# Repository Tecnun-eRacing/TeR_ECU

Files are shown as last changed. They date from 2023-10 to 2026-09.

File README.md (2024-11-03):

# TeR_ECU
TeR Electronic Control Unit, which handles the behaivour of the cars dynamic system while gathering all the sensor and data neccesary for operation through its inputs and communication buses.

## Features
- STM32F405VGTx Microcontroller (Cortex™-M4 Core@168mHz with FPU)
- USB For Diagnosis Operation
- 2x CAN 2.0 For its communication with the Powertrain CAN and main sensors CAN
- NEO M9N GPS modules from u-blox, for determining cars position (Posibility to drive an active Antenna)
- 9DOF IMU consisting in Accelerometer, Gyroscope and Magnetometer for accurate posting and torque algorithms
- 4 Digital Inputs (0V-24V Range)
- 4 PWM Outputs(3.3V), for servo control, including actuators
- 4 Analog Inputs (0V-3.3V) Possibility of configurable Input divider
- 4 Digital Outputs(0V-24V) High side mosfet drivers
- 2 WS2812 RGB Led Channels using integrated SPI for FS-Spain LightShow Acceleration


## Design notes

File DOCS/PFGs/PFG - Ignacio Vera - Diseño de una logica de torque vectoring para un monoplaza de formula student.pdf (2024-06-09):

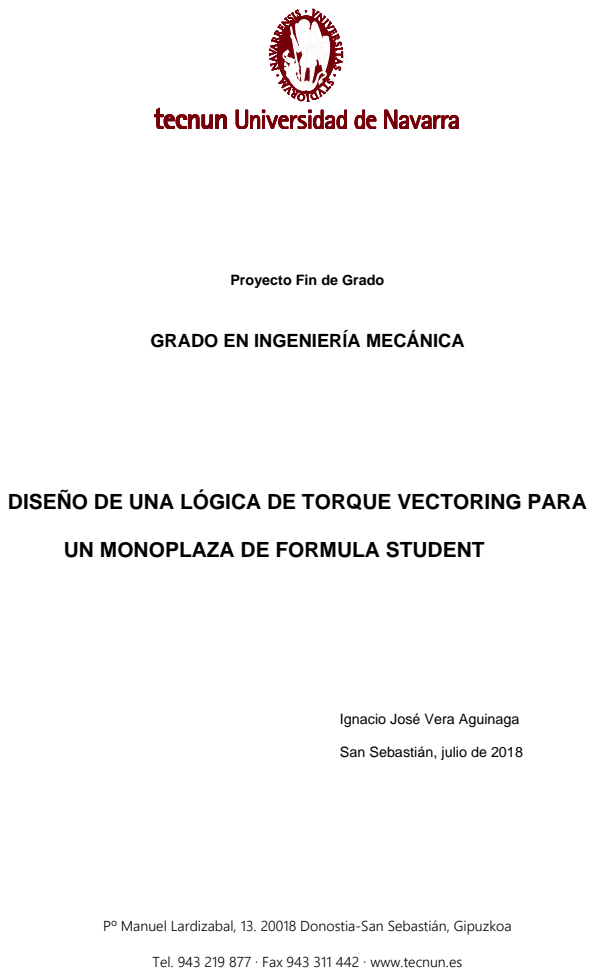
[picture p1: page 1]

Proyecto Fin de Grado

GRADO EN INGENIERÍA MECÁNICA

DISEÑO DE UNA LÓGICA DE TORQUE VECTORING PARA

UN MONOPLAZA DE FORMULA STUDENT

Ignacio José Vera Aguinaga

San Sebastián, julio de 2018

Pº Manuel Lardizabal, 13. 20018 Donostia-San Sebastián, Gipuzkoa

Tel. 943 219 877 · Fax 943 311 442 · www.tecnun.es

Diseño de un Torque Vectoring para un monoplaza de FSAE

Ignacio J. Vera Aguinaga

## AGRADECIMIENTOS

A mi familia, especialmente a mis padres y a mi hermano. Por aguantarme y

sufrirme cada día. Por darme absolutamente todo lo que son y tienen. Por estar a mi lado

incluso cuando las horas de trabajo no me permiten estar al suyo. No habría llegado hasta

aquí de no ser por ellos. Gracias, por todo.

A mis amigos. Por no olvidarse de mí, aunque estuviera desaparecido. Por todos

estos años y los que nos quedan. Gracias.

A los profesores y compañeros que he tenido, desde la Compañía de María,

pasando por SUMMA Aldapeta, la Universidad de Linköping y finalmente Tecnun. De todos

ellos he aprendido y me llevo cosas que hoy me hacen mejor persona. Gracias.

A Iker Aguinaga. Por todos sus consejos y por ayudarme a ver las cosas de otra

manera. Gracias.

A Andoni Medina. Por guiarme en la realización de este proyecto y estar siempre

dispuesto a echarme una mano. El contenido que aquí se recoge habría sido mucho peor

sin su ayuda. Gracias.

A mis amigos y excompañeros de Tecnun Motorsport. Por inculcarme una pasión.

Por los días de taller, y también por las noches. Por ayudarme a crecer en todos los

aspectos. GrAciaS.

A mis amigos y compañeros de Tecnun eRacing. Por mantener viva mi ilusión. Por

darme la oportunidad de realizar este proyecto, que espero que sea de utilidad en el futuro.

Por todo lo que nos queda por lograr y lograremos. Esto es en gran parte para vosotros.

Gracias.

## CONTENIDO

## ÍNDICE DE FIGURAS

Figura 57: Bloque E-Gas E-Motor correspondiente a la asignación de par motor de Carmaker for Simulink

Figura 82: Bloque Wheel Long v estimation | 108
Figura 83: Bloque K parameter | 109
Figura 84: Bloque Sigmoid function | 110
Figura 85: Resultados en la prueba de Endurance de FSG 2017 | 111

## ÍNDICE DE TABLAS

Tabla 1: Valores empleados para el cálculo de yaw rate | 42
Tabla 2: Parámetros del controlador PID | 57
Tabla 3: Presupuesto de inmovilizado | 77
Tabla 4: Presupuesto de material fungible | 77
Tabla 5: Presupuesto de equipamiento | 77
Tabla 6: Presupuesto de software | 78
Tabla 7: Presupuesto de mano de obra | 78
Tabla 8: Resumen del presupuesto | 79

## ÍNDICE DE GRÁFICOS

Gráfico 1: Puntuación FSAE | 17
Gráfico 2: Puntuación FSG | 18
Gráfico 3: Fuerza longitudinal frente a slip ratio (Hoosier R25B 16x6x10) | 32
Gráfico 4: Comparación del yaw rate objetivo y el real (sin TV) | 55
Gráfico 5: Par en los motores del vehículo (sin TV) | 55
Gráfico 6: Comparación del yaw rate objetivo y el real (con TV) | 58
Gráfico 7: Par en los motores del vehículo (con TV) | 59
Gráfico 8: Comparación de velocidades con y sin TV | 59
Gráfico 9: Comparación de aceleración lateral con y sin TV | 60
Gráfico 10: Comparación de % de acelerador pisado por el piloto con y sin TV | 61
Gráfico 11: Comparación del ángulo de giro de volante con y sin TV | 61
Gráfico 12: Comparación del yaw rate objetivo y el real en Skidpad (sin TV) | 63
Gráfico 13: Par en los motores del vehículo en Skidpad (sin TV) | 63

## RESUMEN

Este proyecto nace de la necesidad del equipo de Formula Student Tecnun eRacing

de mejorar continuamente y afrontar nuevos retos para conseguir los mejores resultados

posibles en competición.

En él se desarrolla el diseño de una lógica de torque vectoring. El torque vectoring

consiste en variar la asignación del par entregado a las ruedas de un vehículo de modo

independiente en función de las condiciones de condición, de un modo dinámico. De este

modo, se puede conseguir mejorar el comportamiento general del vehículo y hacerlo más

estable y rápido.

El proyecto se escribe de modo que pueda servir de guía a futuros estudiantes que

quieran profundizar en el campo del control orientado a la dinámica vehicular.

Primero se presentan los conceptos dinámicos básicos que han hecho de base para

el control, así como los requerimientos a nivel de sensorización para implementar un

algoritmo de torque vectoring en un monoplaza de FSAE.

Tras esto se describe en detalle el algoritmo de control empleado: un generador de

referencias de yaw rate que, combinado con un controlador PID, genera un valor de

incremento de par motor que se introduce en los dos motores eléctricos del TeR18. Las

simulaciones del algoritmo, realizadas en IPG Carmaker, muestran una mejora en el tiempo

por vuelta de hasta 1,63 segundos en la prueba de Endurance.

El resultado final del proyecto es un algoritmo de control realizado en Simulink y

listo para ser implementado en el monoplaza de Tecnun eRacing.

## 1 INTRODUCCIÓN

### 1.1 La Formula Student

La Formula Student es una competición internacional entre escuelas de ingeniería,

consistente en formar un equipo de estudiantes para diseñar, fabricar, montar y preparar

un monoplaza de carreras para participar en una serie de pruebas, celebradas en algunos

de los circuitos de automovilismo más célebres del mundo.

La competición de la Formula Student nació de la mano de la SAE (Society of

Automotive Engineering). Conocida como Formula SAE o FSAE, la categoría se desarrolla

en eventos oficiales organizados anualmente.

Figura 1: Logotipo de la SAE

Algunos ejemplos de competiciones oficiales son:

- Formula SAE Michigan, organizado por SAE International
- Formula SAE Australasia, organizado por SAE Australasia
- Formula SAE Italy, organizado por ATA
- Formula Student UK, organizado por IMechE
- Formula Student Austria, organizado por Formula Student Austria
- Formula Student Germany, organizado por FSG e.V.
- Formula Student Spain

Figura 2: Formula Student Germany 2017

Para garantizar unos requisitos de seguridad y buenas prácticas de diseño,

fabricación y mantenimiento, es necesario que los vehículos participantes cumplan una

extensa normativa para poder participar. Antes de que el coche pueda participar en ninguna

prueba dinámica, los jueces de la competición han de acreditar que cumple con dichas

normas.

Esta competición supone una gran oportunidad para estudiantes de ingeniería de

poner en práctica los conocimientos adquiridos en las clases. Además, es también una

oportunidad para acercarse al mundo de la competición del motor.

1.1.1 La competición

Las competiciones de Formula Student valoran tanto aspectos estáticos como dinámicos del monoplaza en los días que dura la competición. Ésta no consiste única y

exclusivamente en hacer rodar el coche para obtener el mejor tiempo posible, sino que

valora y juzga las decisiones tomadas por los estudiantes para lograr su monoplaza.

Los eventos estáticos son todos aquellos eventos puntuables para la clasificación

final que se realizan con el coche parado. Dichos eventos son el Cost Report, un análisis

del coste total del vehículo, el Business Plan, una preparación del presupuesto una

presentación sobre el marketing y finalmente el Design Report, una defensa del diseño del

vehículo completo ante un tribunal especialista en el sector de la automoción.

Los eventos dinámicos son los siguientes: la Acceleration, una carrera de

aceleración en una recta de 75m, el Skidpad, una prueba consistente en dar varias vueltas

a un circuito con forma de “8” para probar el comportamiento del vehículo en situaciones

de alta aceleración lateral y medir su agarre, el Autocross, una prueba consistente en dar

dos vueltas a un circuito revirado que valora la agilidad del vehículo, y la Endurance, una

carrera de resistencia en la que el coche tiene que completar 22 km con un cambio de

piloto a mitad de prueba.

Finalmente, el consumo del coche se valora en la prueba de Efficiency. En esta

prueba se obtienen puntos en función del consumo total de combustible del monoplaza en

la Endurance.

1.1.2 Puntuación de las competiciones

La distribución actual de la puntuación de la competición es diferente en las

competiciones organizadas por la FSAE y las que dependen de la normativa de Formula

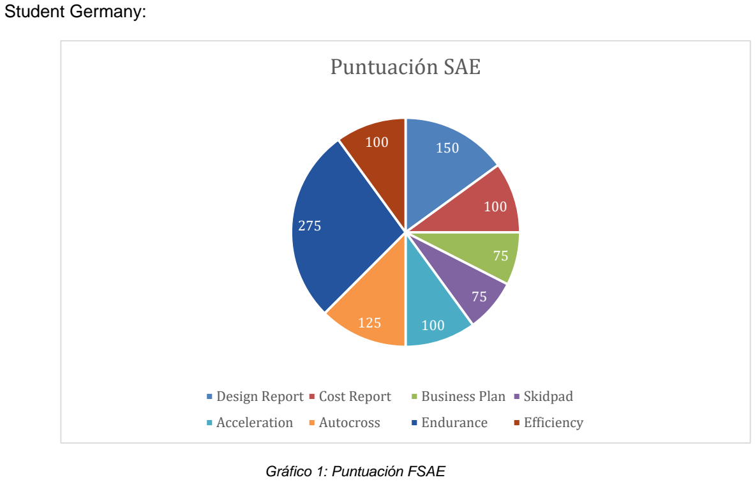
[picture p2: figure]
Student Germany:; Gráfico 1: Puntuación FSAE; Puntuación SAE; Design Report; Cost Report; Business Plan; Skidpad; Acceleration; Autocross; Endurance; Efficiency

Así pues, la máxima puntuación que puede obtener cada equipo es de 1000 puntos.

En ambos formatos el reparto entre las pruebas estáticas y las dinámicas es el mismo,

siendo las pruebas estáticas aproximadamente un tercio de la puntuación total.

1.1.3 Historia de la Formula Student en Tecnun

La Escuela Superior de Ingenieros de la Universidad de Navarra (Tecnun) participa

en la Formula Student desde el año 2009. Con sede en el campus de Ibaeta, San

Sebastián; el equipo Tecnun Motorsport desarrolló anualmente un prototipo para competir

en la disciplina de vehículos de combustión hasta el año 2017. Con sede en el campus de

Miramón, el equipo Tecnun SEED Racing desarrolló un prototipo de propulsión eléctrica

desde 2011 a 2017.

En septiembre de 2017, y de la fusión de los anteriores, nació en Tecnun un nuevo

equipo de Formula Student: Tecnun eRacing. Este proyecto aúna los conocimientos de

Tecnun Motorsport y Tecnun SEED Racing para construir un monoplaza con el que

competir en la categoría de vehículos eléctricos.

Desde que los inicios de la Formula Student en Tecnun han pasado nueve

prototipos diferentes por el Laboratorio de Automoción de la Escuela, y siete por el

Laboratorio de Propulsión Eléctrica, con el objetivo de mejorar el diseño y con ello los

resultados año tras año. Puesto que las necesidades de la competición exigen fabricar un monoplaza desde cero cada año, el factor económico es de una importancia similar al

técnico a la hora de influir en el éxito de un monoplaza. Por esto, el equipo también se

dedica a buscar patrocinadores que puedan servir de apoyo para hacer frente a los costes

del proyecto.

El equipo está formado por alrededor de 50 alumnos bajo la supervisión de un

profesor encargado, organizado en dos departamentos principales, departamento de

organización y departamento técnico. Este último se divide en 6 áreas diferentes. Cada una de ellas, liderada por uno o dos Jefes de Área, se centra en una parte específica del

coche: electrónica de alto voltaje, electrónica de bajo voltaje, chasis, aerodinámica,

transmisión y suspensión.

Monoplazas de la FSAE construidos por Tecnun Motorsport:

Figura 3: Fstec 09 | Figura 4: Fstec 10
Figura 5: Fstec 11 | Figura 6: Fstec 12

Figura 7: Fstec 13 | Figura 8: Fstec 14
Figura 9: Fstec 15 | Figura 10: Fstec 16

Figura 11: Fstec 17

Monoplazas de la FSAE construidos por Tecnun SEED Racing:

Figura 12: e-TEC MKI | Figura 13: e-TEC MKII
Figura 14: Fstec e-III | Figura 15: TSR 14
Figura 16: TSR 15 | Figura 17: TSR 16

Figura 18: TSR17

1.1.4 Tecnun eRacing

Esta temporada, de la unión de medios y capacidades de los equipos Tecnun SEED

Racing y Tecnun Motorsport, ha surgido un nuevo equipo, Tecnun eRacing, dedicado a la

fabricación de coches eléctricos de Formula Student.

Figura 19: El equipo de Tecnun eRacing

Uniendo los conocimientos de electrónica y propulsión eléctrica de Tecnun SEED

Racing y los conocimientos de dinámica vehicular, chasis, suspensión y aerodinámica de

Tecnun Motorsport, el equipo pretende seguir avanzando para obtener cada vez mejores

resultados en las competiciones a las que se presente.

## 2 MOTIVACIÓN Y OBJETIVOS

### 2.1 Motivación

La motivación para la realización de este proyecto es doble. En primer lugar, la

intención de lograr un coche lo más rápido posible que permita que Tecnun eRacing

consiga la mejor puntuación en competición. Como miembro del equipo, es deseo del autor

contribuir a que el monoplaza de Tecnun eRacing cuente con las tecnologías más

avanzadas que le permitan competir al máximo nivel.

En segundo lugar, se pretende abrir una vía al desarrollo de algoritmos de control

cada vez más avanzados y efectivos. La importancia creciente de mecanismos de control

de par en vehículos comerciales (controles de tracción, torque vectoring…) fomenta el

interés en profundizar en el conocimiento de dichas tecnologías.

### 2.2 Objetivos

El objetivo principal de este proyecto es diseñar, probar y validar una lógica de

control que, mediante la técnica de torque vectoring, mejore el desempeño del monoplaza

de Tecnun eRacing en las pruebas dinámicas de las competiciones de Fórmula Student a

las que acuda el equipo. También se trabajará en el desarrollo de un traction control como

complemento al torque vectoring.

Por mejorar el desempeño se entiende disminuir el tiempo en el que el coche realiza

cada prueba, para obtener así un mayor número de puntos y un mejor lugar en la

clasificación de la competición. Así, se considerará que la lógica de torque vectoring

programada es buena si se consiguen los siguientes resultados:

- Disminución de 2 segundos por vuelta el tiempo en las pruebas de Autocross

y Endurance.

- Disminución de 0,3 segundos por vuelta el tiempo en la prueba de Skidpad.

En la prueba de Acceleration el torque vectoring no actúa y no produce ningún

beneficio. Para conseguir disminuir el tiempo en esta prueba sería necesario diseñar un

control de tracción que minimice el deslizamiento de las ruedas del vehículo en aceleración.

Como se detalla más adelante, se ha tratado de diseñar dicha lógica sin éxito.

Podría realizarse un algoritmo capaz de tener un impacto positivo en la prueba de

Efficiency, introduciendo en la lógica los parámetros necesarios para aumentar el par de regeneración de los motores eléctricos del vehículo y minimizar el consumo de energía de

las baterías. Para no introducir una complicación excesiva en el presente proyecto, no se

ha tenido esto en cuenta a la hora de diseñar el TV.

Asimismo, se definen también una serie de objetivos cualitativos que derivan del

uso del torque vectoring:

- Conseguir un coche más sencillo de conducir: cuanto más fácil de entender

sea el comportamiento del vehículo para el conductor, más cómodo se

sentirá con el mismo y le permitirá circular a mayor velocidad y de una forma

más segura. El torque vectoring puede usarse para corregir el efecto

suubvirador o sobrevirador de un vehículo y lograr un coche neutro.

- Mantener el par por debajo del límite de tracción: controlando el par

entregado a cada rueda por debajo del límite de tracción de las mismas, se

asegura que las ruedas motrices no derrapan y por tanto no se

desaprovecha la potencia del vehículo, además de consumirse menos

energía.

## 3 ESTADO DEL ARTE

### 3.1 El torque vectoring

El torque vectoring (TV en forma abreviada) es un sistema para controlar el par en

las ruedas de un automóvil dependiendo de la situación de conducción.

En coches convencionales con motor de combustión interna este efecto se logra

por medio del diferencial. A ambos ejes de salida de un diferencial convencional se coloca

un sistema de discos de embrague accionado por un motor eléctrico y un conjunto de

engranajes. En una curva, los motores eléctricos accionan el embrague de la rueda

exterior, conectando un sistema de engranajes planetarios a la salida del diferencial. Esto

cambia la relación de transmisión en el semieje exterior, aumentando el par enviado a la

rueda exterior.

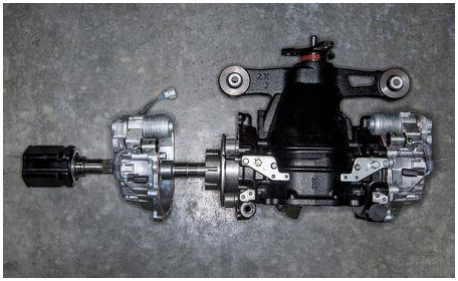
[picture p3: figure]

Figura 20: Diferencial con Torque Vectoring de un Lexus RC F

Esta misma técnica también se emplea en coches con tracción a las 4 ruedas para

regular el par que se envía al eje delantero o al trasero.

En coches eléctricos con más de un motor es más sencillo implementar el torque

vectoring ya que no requiere de ningún componente mecánico adicional: basta con

programar una lógica de control que altere la comanda de par que se envía a cada uno de

los motores.

Figura 21: Imagen del powertrain del TeR18, con dos motores Emrax 188

Además, en comparación con los diferenciales con TV, este sistema ofrece la

ventaja de permitir controlar de un modo mucho más preciso el par que se entrega a cada

rueda.

### 3.2 Torque vectoring en la Formula Student

Algunos de los equipos que participan en la categoría eléctrica de Formula Student

llevan años desarrollando diferentes lógicas de control para coches de tracción a dos o

cuatro ruedas. Principalmente se emplea para lograr tres objetivos:

- Ajustar el yaw rate del vehículo.
- Aumentar la aceleración lateral máxima.
- Controlar el slip ratio de las ruedas tractoras.

### 3.3 Torque vectoring en Tecnun

En los años de historia de la FSAE en Tecnun, se han realizado investigaciones por

parte del equipo Tecnun SEED Racing en el campo del Torque Vectoring, habiéndose

incluso realizado un Trabajo de Fin de Grado sobre la materia.

También se ha probado con sistemas de asignación de par sencillos como introducir

una variación de par proporcional al giro de volante en el monoplaza. Sin embargo, nunca

se llegó a implementar en ninguno de sus vehículos una lógica completa de control.

### 3.4 IPG Carmaker

Para la realización de este proyecto se ha empleado el software IPG Carmaker, de

la compañía IPG Automotive. Es un software popular en la industria del automóvil que

permite simular dinámicamente el comportamiento de un coche previamente modelado en

el programa.

Figura 22: Interfaz gráfica de IPG Carmaker

IPG Carmaker permite la definición de la mayoría de parámetros de un coche:

masas, rigideces, amortiguadores, neumáticos, geometría de suspensión… También es

posible generar un trazado de circuito o modelar características del piloto.

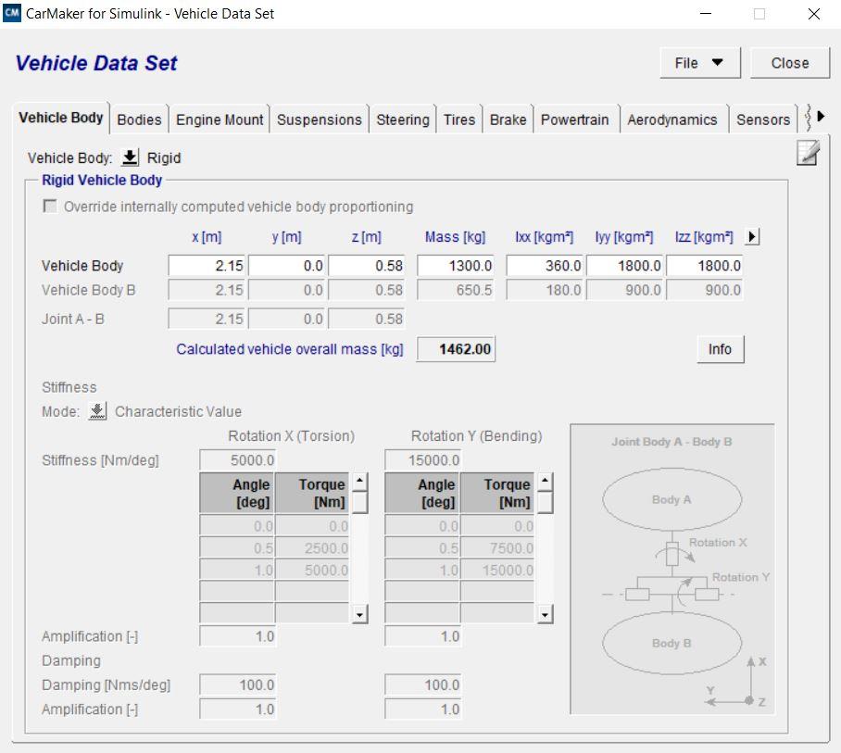
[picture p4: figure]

Figura 23: Muestra de algunos de los parámetros personalizables en Carmaker

En este proyecto se ha utilizado el modelo del TeR18 creado por el antiguo miembro

del equipo Carlos Rubio para su proyecto de Fin de Máster “Parametrization and Simulation

of an Electric FSAE Racecar”.

### 3.5 Simulink

El software elegido para programar la lógica de control ha sido Simulink, de la

compañía Mathworks. Se trata de un software de programación en bloques con una gran

variedad de funciones.

Figura 24: Ejemplo de programa de Simulink

Por ser un entorno basado en Matlab, es totalmente compatible con él, posibilitando

trabajar en Matlab con resultados obtenidos en Simulink.

IPG Carmaker posee una extensión llamada “Carmaker for Simulink”, mediante la

cual se puede trabajar con los modelos de Carmaker desde el entorno de Simulink,

alterando sus parámetros y añadiendo funciones mediante bloques programables. Gracias

a esto ha sido posible modificar el modelo de vehículo del que se disponía para introducir

en él el algoritmo de TV en forma de diagrama de bloques.

## 4 NOCIONES BÁSICAS DE DINÁMICA VEHICULAR

En este apartado se explicarán únicamente los conceptos de Dinámica Vehicular

necesarios para entender los razonamientos seguidos en este proyecto. Para una mayor

profundización en la Dinámica Vehicular, se recomienda acudir a los libros “Fundamentals

of Vehicle Dynamics”, de T. D. Gillespie, y “Race Car Vehicle Dynamics”, de Milliken y

Milliken.

### 4.1 Ejes de referencia

Para ser coherentes con la definición de las ecuaciones en la programación se ha

empleado el sistema de referencia indicado a continuación durante toda la realización del

proyecto:

Figura 25: Ejes de referencia empleados en el proyecto

El eje X coincide con el eje longitudinal del vehículo, siendo el sentido positivo hacia

el frente. El eje Y se encuentra en un plano horizontal, es perpendicular al eje X y pasa por

el centro de gravedad del coche, siendo el sentido positivo hacia la izquierda mirando el

vehículo desde arriba. Por último, el eje Z es el eje vertical que pasa por el CdG y su sentido

positivo se define hacia arriba.

### 4.2 El neumático

4.2.1 Slip ratio y slip angle

El neumático es uno de los componentes más importantes de un automóvil. Al ser

su único punto de contacto con el suelo, es el encargado de transmitir a la pista todas las

fuerzas que impulsan al vehículo en su movimiento.

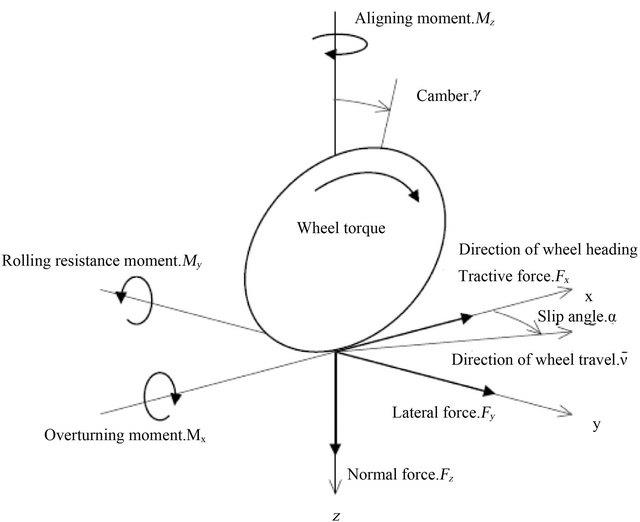
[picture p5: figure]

Figura 26: Fuerzas sobre una rueda

Normalmente, el movimiento de los neumáticos de un coche no es de rodadura

pura. Debido a la deformación que sufren los neumáticos durante el movimiento del

vehículo parte del área de contacto de los mismos desliza mientras la otra posee

movimiento de rodadura

Se define el slip ratio o ratio de deslizamiento como la relación entre la velocidad

angular real que posee una rueda y la que tendría en un movimiento de rodadura perfecta.

Hay diferentes maneras de definir el slip ratio, pero la empleada en este proyecto ha sido

la definida por la SAE:

SR =

ω × rw
v

− 1

Otro parámetro importante a definir es el slip angle o ángulo de deriva de una rueda,

el ángulo entre la dirección en la que apunta una rueda y la dirección en que realmente se

mueve. Este fenómeno ocurre debido a las deformaciones sufridas por el área de contacto

del neumático al ser sometido a una fuerza lateral.

Estos dos parámetros tienen una influencia directa y fundamental en las fuerzas

longitudinales y laterales que experimenta el vehículo. Para entender esto se explicará el

modelo de neumático.

4.2.2 Modelo de neumático

A finales del siglo XX Hans B. Pacejka desarrolló un modelo matemático capaz de

describir el comportamiento de un neumático en función de diversas variables, que se

conoce como “Fórmula Mágica de Pacejka”. Este modelo se ha ido actualizando en

distintas versiones y su uso está muy extendido. Con él se pueden calcular las principales

fuerzas que afectan a un neumático: longitudinal, lateral, combinadas, momento

autoalineante…

El modelo más avanzado tiene en cuenta las siguientes variables:

- Fuerza vertical
- Slip angle
- Slip ratio
- Camber angle
- Presión del neumático

Además, el modelo posee alrededor de 100 parámetros con significado físico propio

para caracterizar con precisión las propiedades de cada tipo de neumático.

Para realizar el modelo de los neumáticos se emplean los datos obtenidos por el

Tire Test Consorcium (TTC) y el software Optimum Tire. El TTC es una organización

dependiente de la SAE que nació de la necesidad de los equipos de Formula Student de

disponer de datos precisos sobre el comportamiento de sus gomas. Se dedica a testear

diferentes tipos de neumáticos de posible uso en competiciones FSAE para publicar los

resultados en una base de datos puesta a la venta.

El equipo dispone de un modelo de los neumáticos Hoosier R25B 18x6 - 10

realizado por Carlos Rubio. Aunque los neumáticos finalmente empleados en el monoplaza

han sido los Hoosier R25B 18x7,5 - 10 (1,5 pulgadas más anchos), de estas gomas no se

poseen datos por no haberse publicado los resultados del test TTC en el momento de la

realización del proyecto. Por tanto, se utilizará el citado modelo.

Gráfico 3: Fuerza longitudinal frente a slip ratio (Hoosier R25B 16x6x10)

En la imagen se observa cómo cambia la fuerza longitudinal que el neumático ejerce

sobre la pista en función del slip ratio de la rueda. Se observa que existe una zona alrededor

del 0 en la que el comportamiento es lineal, tras la cual el neumático se satura y alcanza

el valor máximo de fuerza que es capaz de transmitir. Tras este pico, el valor de Fx

disminuye ligeramente.

Dicho pico de fuerza suele estar situado en valores cercanos al 0,1 o 0,12 de slip

ratio, siendo el valor de pico exacto diferente para cada neumático. El slip ratio se calcula

con la velocidad en rueda, con lo que puede ser alterado mediante el par motor, y por tanto

es posible controlarlo mediante el traction control para mantener su valor cerca del punto

óptimo.

La fuerza lateral que soporta un neumático es principalmente función del slip angle

al que se ve sometido.

### 4.3 Círculo de fricción

Se denomina círculo de fricción al círculo ficticio cuyo radio es del valor de la fuerza

máxima que una rueda es capaz de soportar en cada dirección. Esta figura no es circular

en realidad, pero en muchos trabajos se simplifica y se toma por una forma circular.

Figura 27: Dibujo del círculo de fricción, con una fuerza de ejemplo

Los límites de agarre de un vehículo se calculan con el coeficiente de fricción

neumático-asfalto:

Fmax = μ × Fz

Por tanto, son función de la carga vertical sobre la rueda. No se explicará en esta

memoria las transferencias de carga vertical que experimenta un coche en su movimiento,

pero sí se resalta que, si se conoce el valor de la carga vertical, se puede tratar de estimar

los límites de agarre de cada rueda. Si al mismo tiempo se conocen las fuerzas longitudinal

y lateral reales en cada neumático, se puede determinar la fuerza extra que se puede

aplicar a cada rueda mediante la modificación del par motor para acercarse lo máximo

posible a dicho límite sin superarlo.

### 4.4 Comportamiento lateral de un vehículo

Como se ha explicado anteriormente, el TV es un recurso para la mejora del

comportamiento de un vehículo al tomar una curva. Por tanto, se explicarán a continuación

los conceptos necesarios para tener unas nociones básicas sobre el comportamiento de

un coche en curva.

4.4.1 Yaw angle y yaw rate

Se llama yaw angle al ángulo entre el eje longitudinal (x) del coche y un eje de

referencia en el plano xy. Por tanto, el yaw rate es la velocidad angular con la que cambia

este valor, es decir, la velocidad con la que el vehículo pivota alrededor de su eje Z. Al

tomar una curva, un coche posee una velocidad de yaw además de una velocidad

longitudinal y lateral. El yaw rate se calcula como sigue:

YR =

v
R

4.4.2 Modelo de bicicleta y ecuación de Ackerman

En dinámica vehicular, es habitual emplear una simplificación consistente en

considerar el automóvil como un vehículo de sólo dos ruedas, una delantera y una trasera.

De esta simplificación, conocida como modelo de bicicleta, se deducen algunas

expresiones de gran importancia para el análisis del comportamiento de un vehículo.

Figura 28: Esquema del modelo de bicicleta

Desarrollando las relaciones geométricas entre ángulos de la Figura 28 se puede

hallar una relación para calcular el giro de rueda necesario para negociar una curva:

δ =

L
R

+ (αf − αr)

Siendo L la batalla del coche, R el radio de la curva y αf y αr los slip angles delantero

y trasero respectivamente. Esta ecuación se puede desarrollar aún más realizando un equilibrio de momentos y mediante la relación existente entre la fuerza lateral del neumático

y el slip angle.

δ =

L
R

+ K × ay

Siendo K el gradiente de subviraje, un parámetro característico de cada vehículo

que puede determinarse experimentalmente.

4.4.3 Subviraje y sobreviraje

Se llama subviraje al efecto que se produce cuando un vehículo gira menos de lo

comandado por su conductor. Al caso contrario se lo denomina sobreviraje. Ambos son

efectos indeseados en la conducción.

Cuando el slip angle de las ruedas delanteras es mayor que el de las traseras, o lo

que es lo mismo, cuando K>0, un coche de batalla L necesita un mayor ángulo de giro para

tomar una curva de radio R, y se produce el efecto de subviraje. Cuando el slip angle de

las ruedas traseras es mayor que el de las delanteras (o K<0), un coche de batalla L

necesita un menor ángulo de giro para tomar una curva de radio R, y se produce

sobreviraje.

Figura 29: Subviraje y sobreviraje

Si K=0, el vehículo es neutro y, teóricamente, responde a las comandas de giro

recibidas sin desviaciones.

## 5 SENSORIZACIÓN DEL VEHÍCULO

El presente proyecto se centra en el diseño del torque vectoring, pero para posiblitar

su implementación en el monoplaza es indispensable tener unas nociones básicas sobre

los sensores que permitirán recibir la información necesaria para el funcionamiento del

algoritmo de control, así como del controlador en el que se introducirá la lógica.

La líder del área de Electrónica de Tecnun eRacing, Paula Martínez, será la

encargada de implementar el TV en el TeR18 dentro del marco de su PFG. Para ello

empleará un microcontrolador TMS320F28377S en una placa comercial, que puede ser

programado en lenguaje Simulink. Este controlador lee la información necesaria de los

sensores del vehículo por comunicación CAN. La señal del sensor inercial es leída por el

dispositivo UART.

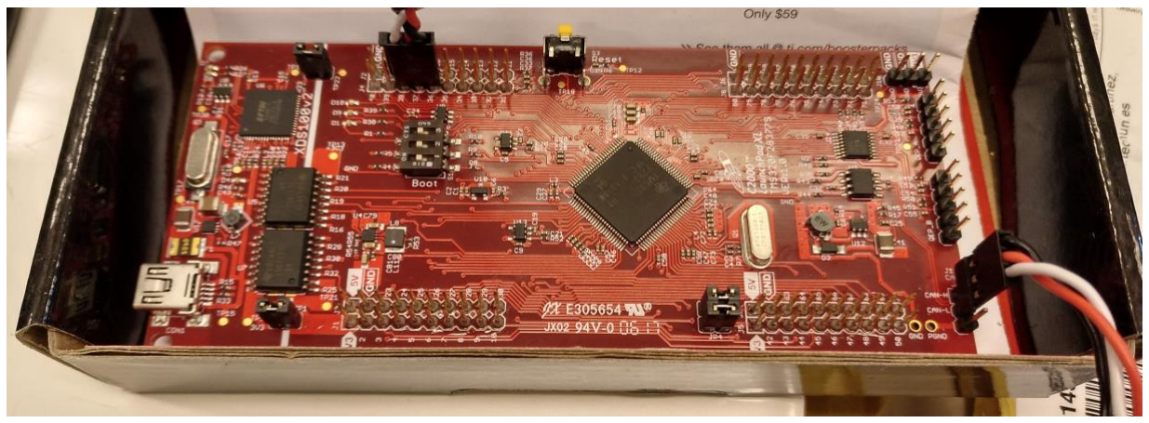
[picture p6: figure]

Figura 30: Placa comercial en la que se implementará el torque vectoring en el TeR18

Para obtener la información necesaria del vehículo en cada momento, se emplearán

los siguientes sensores:

- Sensor de giro de volante: este sensor viene integrado en la cremallera de

dirección, modelo Zedaro zRack 262. Se trata de un potenciómetro

conectado al eje que introduce el giro de la columna de dirección a la

cremallera. Por tanto, es capaz de medir el giro de esta última.

Figura 31: Sensor de giro de volante

- Inertial measurement unit (IMU): la IMU es un sensor capaz de medir

aceleraciones y velocidades, tanto lineales como angulares, en los tres ejes

de referencia del coche. En la imagen el sensor aparece en la posición en

la que se encuentra en el monoplaza: con los ejes en la orientación deseada.

Figura 32: Sensor inercial (IMU)

- Sensores de posición del acelerador: por normativa, se colocan en el pedal

del acelerador dos sensores de posición, que determinan la comanda de par

que es necesario enviar a los inversores.

Figura 33: Sensores de posición del acelerador

Estos son los sensores básicos para diseñar una lógica de torque vectoring efectiva.

Otros sensores que pueden instalarse para introducir funciones adicionales en la lógica

son:

- Sensor de presión de freno: mediante este sensor puede calcularse el par

de frenado en las ruedas traseras y alterar la comanda de par en

consecuencia, para que el par motor no trabaje contra los frenos.

Figura 34: Sensor de presión de freno

- Sensor de velocidad angular de motor/rueda: mediante estos sensores

puede calcularse el slip ratio de las ruedas o la potencia en las mismas,

conocida la comanda de par del motor. Los motores Emrax 188 que monta

el TeR18 llevan un sensor de velocidad integrado que puede usarse para

calcular la velocidad en las ruedas traseras con la relación de transmisión.

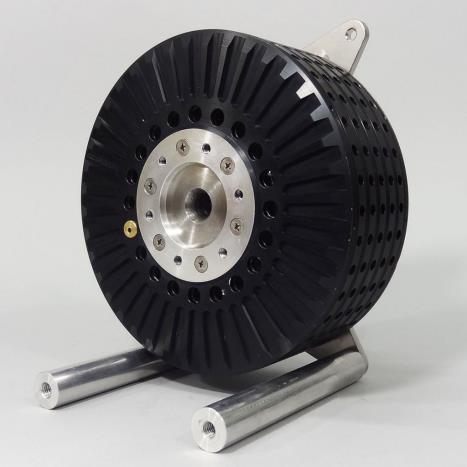
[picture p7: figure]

Figura 35: Sensor de velocidad en rueda | Figura 36: Motor Emrax 188
- | Galgas | extensiométricas | en | push/pull | rods: | instalando | galgas

extensiométricas para medir la deformación de los push rods de suspensión

pueden conocerse las cargas verticales en cada rueda en tiempo real. Este

dato es necesario para calcular las fuerzas en cada rueda usando el modelo

de neumático. La carga vertical también se puede determinar mediante

cálculos de dinámica vehicular.

Figura 37: Galgas extensiométricas en un test del Ferrari F138 (2013)

## 6 SISTEMA DE CONTROL

Durante la realización de este proyecto se han barajado distintas lógicas y

diferentes métodos para lograr los objetivos descritos en el apartado 2 de esta memoria.

Todos ellos se basan en la modificación de la señal de comanda de par, que se origina en

el sensor de posición del pedal del acelerador, accionado por el piloto.

Esta señal se puede interpretar en forma de tanto por 1, siendo 0 el valor cuando el

pedal no está siendo pisado y 1 cuando el piloto está acelerando a fondo. La lógica recibe

esta señal del pedal y la duplica, generando dos señales iguales del mismo valor que la

original. Después modifica cada una de esas dos señales de distinta manera para

finalmente enviar cada una a una rueda determinada.

La modificación de ese valor se realiza siguiendo el siguiente esquema:

Figura 38: Esquema del funcionamiento del sistema de control

Es importante respetar este orden y modificar la señal de par en función de las

solicitaciones en curva antes de modificarla para obtener el slip deseado. La razón para

esto es que, si se aplica el torque vectoring tras el traction control, es prácticamente

inevitable deshacer el efecto de control de slip dado por este último. Además, aplicando

primero el torque vectoring, puede estimarse la velocidad en cada rueda que el par motor

ya alterado conseguirá, usarse esa estimación para calcular el slip que tendrá cada

neumático contando la acción del TV y controlarlo.

## Datos de entrada

- Parámetros del
vehículo
(características
de la planta)
- Sensores (inputs
del piloto y
variables de
funcionamiento)

## Torque Vectoring

- Asignación del
par en rueda en
función de la
necesidad de
mejorar el
comportamiento
en curva

## Traction Control

- Corrección del
par obtenido en
el TV para cada
rueda para
conseguir la
máxima Fx o
evitar el
deslizamiento de
la rueda

### 6.1 Torque vectoring

La lógica de torque vectoring empleada consiste en la generación dinámica de un

valor de referencia de yaw rate que después se compara con el yaw rate real. Tras esto, el

error entre ambos es introducido en un PID cuya salida se traduce en incremento de par

motor, para tratar de aproximar el valor real de yaw rate a la referencia calculada

dinámicamente.

Los diagramas de bloques de Simulink correspondientes al TV se incluyen en el

anexo A1.

6.1.1 Cálculo del yaw rate ideal

Para este cálculo se emplean varios parámetros del coche y la información recibida

por diferentes sensores. Los datos necesarios son los siguientes:

Señal | Significado | Sensor | Valor
Gas | Porcentaje de acelerador pisado | Sensor de posición del pedal del acelerador | -
Ax | Aceleración longitudinal | IMU | -
Ay | Aceleración lateral | IMU | -
SteerAngle | Grados de giro del volante | Sensor de giro de volante | -
YawRate | Yaw rate | IMU | -
v | Velocidad | IMU | -
TVenable | Activador del TV | - | 0 o 1
Wheel rad | Radio de la rueda | - | 0,127 m
Wheelbase | Batalla del coche | - | 1,58 m
Track r | Ancho de vía trasero | - | 1,18 m
Gear ratio | Relación de transmisión en la reductora | - | 5
Steer Rack reduction | Relación desplazamiento cremallera – giro de volante | - | 5,25 mm/º
Steer TRod-Kingpin dist | Distancia del punto de anclaje del brazo de dirección en la mangueta al punto del eje de kingpin que está en el mismo plano horizontal | - 60 mm

Tabla 1: Valores empleados para el cálculo de yaw rate.

El cálculo se realiza de siguiente modo:

YRref =

v
L

× (δ − K × ay)

Donde:

- v es la velocidad del coche [m/s]
- L es la batalla del vehículo [m]
- δ es el ángulo de giro de la rueda [º]
- K es el gradiente de subviraje objetivo, elegido por el programador
- ay es la aceleración lateral del vehículo [g]

El valor δ se obtiene a partir del ángulo de giro de volante y las relaciones

geométricas de los movimientos de la dirección: al girar el volante se desplaza la

cremallera, lo que a su vez desplaza el conjunto de rueda haciéndolo pivotar alrededor del

eje de kingpin. El centro de pivotamiento es el punto del eje de kingpin que se encuentra

en el mismo plano horizontal que el anclaje del brazo de dirección a la mangueta, por lo

que el cálculo se realiza del siguiente modo:

δ = sin⁻¹ (

θ × StRack red
dist TRodKingpin)

Siendo θ el ángulo de giro de volante en grados.

Como el valor recibido de los sensores de ángulo de volante y aceleración lateral

viene dado en radianes y en m/s²
, respectivamente, hay que multiplicarlo por las

transformaciones correspondientes para operar con ellos en grados y g’s.

Este valor de referencia se multiplica después por una función de transferencia que

modela el tire relaxation length, el retraso temporal que se produce entre que la rueda

adquiere un slip angle determinado y la fuerza lateral del neumático adquiere un valor

estacionario. La función utilizada en el código es la definida en Carmaker para el relaxation

length.

6.1.2 Controlador PID

El valor de referencia de yaw rate, obtenido como se explica en el apartado anterior,

se resta después a la señal de yaw rate real para obtener el error en yaw, que será la señal

de entrada del controlador. El objetivo de todo este bloque de la lógica de control es

minimizar este error lo máximo posible, tratando de convertirlo en 0, ya que eso significará que el yaw rate real se aproxima lo máximo posible a la referencia calculada. Si el yaw rate

real es menor que la referencia es porque el coche subvira, mientras que si el yaw rate real

es mayor que la referencia el coche sobrevira.

Para ello se utiliza un controlador PID. Se ha optado por construir el controlador con

un sistema de bloques sencillos en vez de utilizar el bloque de controlador PID por defecto

de Simulink para lograr una mejor comprensión del controlador: poder construir el sistema

desde cero, visualizar la magnitud de cada una de sus señales, analizar mejor cómo

cambian al alterar sus parámetros…

El PID es un controlador que actúa en función a tres señales: el error, su integral y

su derivada. La primera de ellas proporciona una corrección mayor o menor según sea la

diferencia entre la referencia y el valor real mayor o menor, respectivamente. Si el error

alcanza un valor estable distinto de cero, la componente integral del controlador actúa para

tratar de reducirlo, y si la referencia varía mucho respecto del valor real en un período corto

de tiempo, la acción derivativa contrarresta ese cambio en el error.

Para visualizar las tres componentes de la forma más clara posible, se emplea la

forma paralela del controlador:

u(t) = Kp ∗ e(t) + Ki ∗ ∫ e(t) + Kd ∗

d [e(t)]
dt

Y, además, se definen

Ki =

Kp
Ti

Kd = Kp ∗ Td

Donde Ti y Td son el tiempo integral y derivativo, respectivamente. Definiendo estos

valores se definen también las ganancias integral y derivativa, como se muestra en las

fórmulas anteriores.

Las ganancias Kp, Kd y Ki definen la intensidad de las acciones proporcional, integral

y derivativa, aumentando o disminuyendo los efectos correctivos de cada una.

Para la acción integral se ha introducido además una función anti-Windup. El efecto

Windup ocurre cuando se da un cambio brusco en la referencia (cambio grande de valor

en un corto período de tiempo). Consiste en el aumento excesivo del valor de la acción

integral, provocando una salida del controlador demasiado elevada. Esto conlleva la aparición de un sobreimpulso que, si es demasiado grande, además de alejarnos de la

referencia puede provocar daños en el dispositivo actuador.

Figura 39: PID con anti-Windup

Para eliminar este efecto, las lógicas incluyen una serie de operaciones que

conforman la función anti-Windup: se introduce tras la suma de las tres señales una

saturación, y se resta el valor previo a la saturación a su valor posterior. Esta nueva señal

se multiplica por una ganancia y se suma al valor de la acción integral antes de su

integración. Si la actuación no supera el valor marcado por los límites de la saturación la

acción correctiva del anti Windup es 0, ya que la señal antes y después de la saturación

son del mismo valor y se anulan al restarlas.

De este modo, si el valor de la acción integral se dispara, la saturación limita el valor

de la suma de las tres acciones al valor máximo de actuación deseado. La señal sin saturar

se resta a la saturada, resultando una señal de valor muy alto y negativo que se multiplica

por una ganancia Kb y después se suma a la acción integral para devolverla a valores

normales (más bajos) en la siguiente iteración.

A continuación se explica de modo esquemático su funcionamiento:

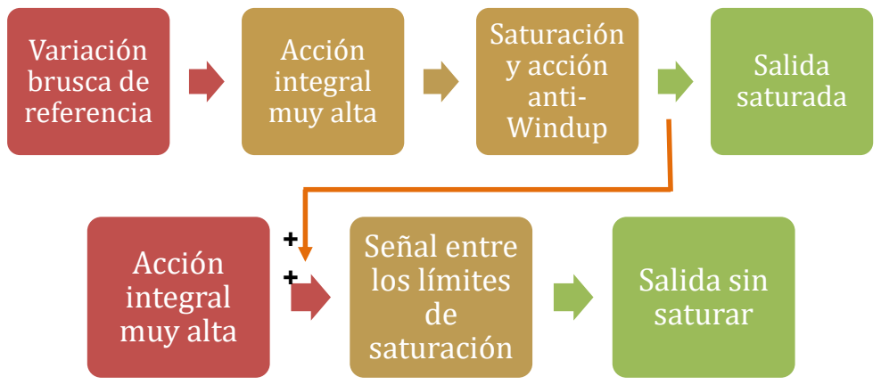
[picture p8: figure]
Variación brusca de referencia; Acción integral muy alta; Saturación y acción anti- Windup; Salida saturada; Señal entre los límites de saturación; Salida sin saturar

Figura 40: Esquema explicativo de la función anti-Windup

En la acción derivativa es necesario instalar un filtro para que la señal no presente

picos que distorsionen el valor de la actuación. Como la lectura que proviene de los

sensores tiene ruido, el valor del yaw rate real y el de referencia (calculado con datos de

sensores) también presentarán este ruido y por ende también aparecerá en el error. Por

tanto, la derivada de esta señal serán picos muy grandes de alta frecuencia.

Para eliminar estos picos, se instala un filtro pasa-baja a la salida del derivador,

precedido de una ganancia. La señal filtrada se resta de nuevo a la salida del derivador, y

se manda a la actuación la salida de la ganancia, como se muestra en el esquema:

Figura 41: Esquema de un PID con filtro derivativo

1

2

6.1.3 Controlador feedforward

El feedforward es un controlador que proporciona una señal de respuesta

puramente proporcional a la referencia o a la perturbación del sistema. En este caso, se

introdujo para poder tener un control de la respuesta dependiente de la referencia de yaw

rate además de tener uno proporcional al error.

Figura 42: Esquema de un controlador feedforward en paralelo con un controlador feedback

En caso de querer anular el controlador feedforward, basta con definir su ganancia

como 0.

6.1.4 Cálculo del incremento de par en rueda

El PID y el feedforward se tunearán de modo que su salida sea directamente un

valor en Nm, el incremento de Mz necesario para conseguir el yaw rate objetivo. Este valor

se transforma en incremento de par en rueda mediante una serie de sencillas operaciones.

Primero, se transforma el incremento de Mz necesario en incremento de Fx

necesario, dividiéndolo entre la mitad de la longitud del eje trasero. Desarrollando un poco

la expresión:

Inc Fx =

2 × Inc Mz
tr

Se podría considerar que el incremento en Mz se consigue aumentando la fuerza

en sólo una de las ruedas del vehículo. Sin embargo, esto podría significar la introducción

de un par excesivo en una de las ruedas, lo cual podría hacer derrapar esa rueda o incluso

dañar el propio motor al exigirle transmitir un par demasiado alto.

Por tanto, se opta por definir un nuevo incremento objetivo de fuerza longitudinal

como la mitad del anterior, y sumarlo en la rueda exterior y restarlo en la interior. De este

modo se obtiene un incremento total de Mz equivalente al que se obtendría sumando todo

el par en la rueda exterior disminuyendo el riesgo de que ocurran los incidentes antes mencionados. Otra ventaja de optar por esta estrategia es que, al disminuir la fuerza

longitudinal en la rueda exterior, estará más lejos del valor de fuerza combinada para el

cual el neumático pierde agarre. Por tanto, será capaz de absorber más fuerza lateral al

tomar una curva, aumentando la aceleración lateral del coche. Así,

Inc Fx ′ =

Inc Fx
2

Multiplicado por el radio de la rueda, se obtiene el valor necesario de par en rueda

del vehículo:

Inc Tw = Inc Fx ′ ∗ rw

Y para finalizar, dividiendo el valor del par en rueda entre la relación de transmisión

se obtiene el par motor que hay que sumar a la rueda exterior y restar a la interior.

Inc Tm =

Inc Tw
GR

Para poder sumar siempre el par a la rueda exterior y restarlo a la exterior

indistintamente de si son la rueda izquierda o derecha en cada caso, se utiliza el criterio de

signos definido en el apartado 4 y se aprovechan los signos de las lecturas obtenidas por

los sensores. Así, como el criterio utilizado implica que al tomar una rotonda los signos de

todos los parámetros son positivos, el incremento de par motor se suma a la rueda derecha

y se resta a la izquierda, porque la derecha es la rueda exterior al tomar una rotonda. Así,

si la curva es a derechas (sentido contrario a la toma de una rotonda), el incremento de par

motor será negativo y el par se sumará en la rueda izquierda y se restará en la derecha.

También se ha colocado un filtro pasa-baja en la señal de incremento de par, para

evitar que se den transferencias bruscas de par entre los dos motores del coche mientras

está en marcha.

Cabe destacar que todos los efectos se han descrito teniendo en cuenta que el

coche subvira y por tanto el error en el PID es positivo. Si el coche sobrevirase, el error

sería negativo y los incrementos de par se darían en sentido contrario.

Además, se ha introducido una medida de seguridad al incremento de par del torque

vectoring: un enable en forma de puerta lógica que devuelve 0 si el piloto no está pisando

el acelerador y 1 si lo está haciendo. De este modo, si el piloto no quiere recibir la asistencia

del torque vectoring en curva o considera que el incremento de par es excesivo, basta con que levante el pie del acelerador para desactivar su efecto. Esta señal se multiplica por el

incremento de par motor justo antes del filtro de la salida.

### 6.2 Traction control

Para el control de slip ratio de las ruedas traseras, posterior al control de yaw rate,

se ha probado con diferentes aproximaciones. A pesar de no haber logrado ningún

resultado positivo, en este subapartado se describen brevemente tres de los enfoques que

se han probado para ello por su interés académico. Los diagramas de bloques de estos

algoritmos se encuentran en el anexo A2.

6.2.1 Lógica 1: Control de ax

Esta primera aproximación partía de la idea de que, si el coche está traccionando

correctamente, la aceleración longitudinal y la aceleración angular de las ruedas del mismo

están relacionadas.

Por tanto, usando un controlador PID, se trató de controlar el valor de la aceleración

angular de las ruedas traseras, generando un incremento de par motor que se sumaba en

ambos motores.

6.2.2 Lógica 2: Control de slip ratio

Este enfoque se centra en el control del slip ratio de las ruedas traseras del coche

mediante dos controladores PID, para que su valor se mantenga cercano a aquel que da

mayor Fx.

Para decidir el valor de referencia del slip ratio se ha acudido a las curvas del

neumático que posee el equipo (Gráfico 3) y se ha observado que la máxima fuerza

longitudinal se da en torno al valor 0,12 de slip ratio.

Para ello, se realizaba el cálculo del slip en varios pasos. Primero, se calculaba la

carga vertical en cada rueda, utilizando los datos obtenidos mediante sensores y

ecuaciones de dinámica vehicular. Después se calculaban los valores de aceleración

angular con las comandas de par motor previamente alteradas por el TV y se introducían

en un estimador de velocidades que calculaba la velocidad angular de las ruedas traseras

integrando esas aceleraciones angulares.

Con ese valor de velocidad obtenido se calculaba después el slip ratio de las

ruedas, mediante la ecuación del slip ratio definida en el apartado 4. Tras esto venían los controladores PID, que generaban el par correctivo necesario para aproximar el slip

calculado al deseado.

6.2.3 Lógica 3: Limitación del par motor

Este algoritmo está inspirado en la publicación “Improvement of Lap-Time of a Rear

Wheel Drive Electric Racing Vehicle by a Novel Motor Torque Control Strategy” de J.

Ghosh, A. Tonoli y N. Amati.

En él, los autores proponen, primero, establecer una saturación dinámica que limite

el par motor según las condiciones de conducción para no exceder los límites del círculo

de fricción, y tras esto, el uso de un Sliding Mode Controller para aproximar el valor de slip

ratio calculado al deseado.

6.2.4 Descarte de las lógicas de traction control

Tras numerosas simulaciones, se ha comprobado que las lógicas de control de

tracción diseñadas no sólo no disminuyen, sino que aumentan el tiempo por vuelta del

vehículo.

Por tanto, dada la necesidad de disponer de un algoritmo enteramente fiable con

tiempo suficiente para ser testeado, se ha optado por no implementar en el monoplaza

estas lógicas de control de tracción por el momento, hasta su refinamiento.

Se cree que esta ausencia de resultados positivos es debida a fallos en la definición

de los cálculos de las lógicas, ya que los valores calculados en algunas de ellas no

coinciden con los valores devueltos por el software. También podría deberse a que el

software realiza los cálculos teniendo en cuenta más efectos físicos de los que por

simplicidad se han tenido en cuenta en este proyecto.

### 6.3 Incremento del par motor

Una vez calculados los incrementos de par necesarios para lograr los efectos

deseados, se modifica la comanda de par que se enviará a los inversores para lograr dichos

pares.

La señal del pedal del acelerador se traduce fuera de la lógica en % de pedal del

acelerador pisado, y sabiendo que el par máximo nominal que los motores pueden entregar

es de 50 Nm, multiplica la señal de % de acelerador por una ganancia de 50. De este modo, si el pedal está completamente pisado, esto se traducirá en una comanda de par de 50

Nm.

Esta señal se desdobla en dos señales del valor de la original que irán cada una a

uno de los inversores. A cada una se le suma o resta el valor del incremento de par

calculado en los apartados anteriores y se vuelve a realizar la transformación a % de

acelerador dividiendo el resultado entre 50. Esta será la salida de la lógica, que irá al mapa

motor programado en los inversores vía comunicación CAN.

Es posible que, si el piloto está acelerando a fondo y el control actúa, se envíe a un

inversor una comanda de par de más de 50 Nm. Esto no supone un problema ya que los

motores Emrax 188 de los que dispone el TeR18 son capaces de dar un par de pico de

hasta 100 Nm.

### 6.4 Preparación de la simulación

Como la lógica de control necesita de datos de sensores para realizar sus cálculos,

es necesario definir de algún modo las entradas del sistema. Carmaker for Simulink cuenta

con un bloque llamado “Read CM dict” que permite leer cualquier dato de la simulación

mientras se produce, tanto relativos al estado dinámico del coche como comandas del

piloto.

Estos bloques sustituyen a los sensores del vehículo, pero no modelan dichos

sensores: el ruido electromagnético, posibles calibraciones erróneas u otros modos de fallo

son situaciones que no se tienen en cuenta en la simulación en Carmaker.

Es necesario comparar los resultados de las simulaciones de modo cualitativo, para

lo cual se van a emplear tanto el tiempo por vuelta, obtenido de Carmaker, como otras

variables registradas en Matlab durante la simulación: velocidad, aceleración… La

comprobación de que el controlador realiza correctamente su función se llevará a cabo

comparando la señal de yaw rate objetivo y la señal real.

Para guardar el valor de una señal desde Simulink, basta con colocar un bloque

“Save to Workspace” cuya entrada sea la señal a registrar y asignarle un nombre para que

lo guarde como variable de Matlab. Para poder trabajar con estas variables de modo más

sencillo, se accede a las opciones del bloque y se escoge guardarlas como variables de

tipo “array” en el Workspace.

En caso de querer visualizar directamente varias señales y compararlas, puede

emplearse el bloque “Scope” de Simulink o la herramienta “Simulation Data Inspector”. Esta

última permite visualizar señales de distintas simulaciones en un mismo gráfico.

Para llevar a cabo el análisis, se ha colocado un bloque “To Workspace” en las

señales de aceleración lateral, velocidad, ángulo de giro de volante y pedal del acelerador.

Además, se han colocado tres bloques “Scope”: uno para mostrar el yaw rate objetivo y el

real y así poder comprobar que el controlador funciona correctamente, otro para visualizar

el par el cada uno de los motores y un último para observar el valor de las señales del PID

y poder analizar su contribución al valor de la actuación.

Por último pero no menos importante, Carmaker dispone de una función llamada

“Driver Adaption” que es necesario ejecutar cada vez que se realiza algún cambio en el

modelo del vehículo. Esta función inicia un cómputo que adapta el modelo de conductor

para que pueda llevar el coche a sus condiciones límite de funcionamiento, esto es, para

sacar el máximo del coche. El uso de esta función es necesario si realmente se desea ver

la mejora del coche en condiciones de máxima exigencia como son las condiciones de

competición.

### 6.5 Ejecución y análisis de las simulaciones

Las simulaciones se han llevado a cabo principalmente en dos escenarios distintos:

un circuito que pretende emular un circuito de Autocross y Endurance, revirado y sin

muchos tramos rectos, y un circuito reglamentario de Skidpad.

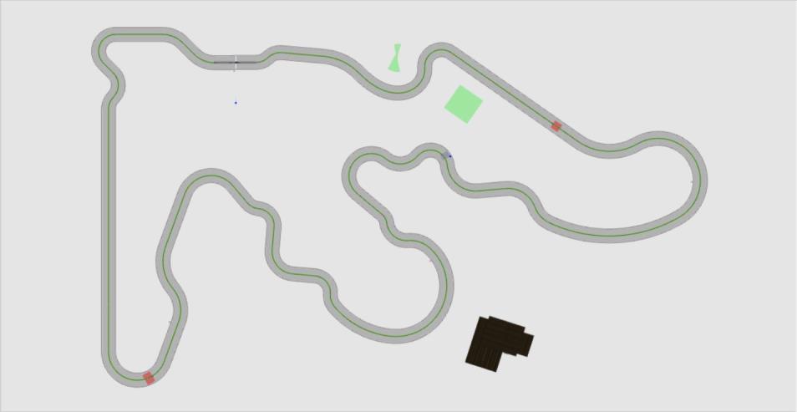
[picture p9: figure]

Figura 43: Circuito empleado para las simulaciones de Endurance y Autocross

Figura 44: Esquema de un circuito de Skidpad con las medidas reglamentarias

Además, se han realizado varios test ISO 4138. El test ISO 4138 consiste en

acelerar el vehículo en línea recta hasta alcanzar una velocidad determinada (60 km/h, en

las simulaciones realizadas), y manteniendo esa velocidad constante, girar el volante

progresivamente para observar el comportamiento del vehículo en función de la

aceleración lateral que soporta. Al acercarse al límite de aceleración que el vehículo puede

soportar, el comportamiento del coche pasa a ser marcadamente subvirador o

sobrevirador.

Como se ha mencionado anteriormente, también se han realizado algunas

simulaciones en una pista de Acceleration que sólo han servido para descartar las lógicas

de Traction Control. Esos resultados no se recogen aquí.

6.5.1 Análisis de Autocross y Endurance

Primeramente, se ha llevado a cabo una simulación del comportamiento del

monoplaza sin el Torque Vectoring activo, para disponer de una base con la cual comparar

los resultados.

Figura 45: Simulación del TeR18 en Endurance (sin TV). Se señala en rojo el tiempo por vuelta

En la parte inferior izquierda de la imagen se puede apreciar el tiempo por vuelta

en la simulación. Se observa que el coche tarda 58,33 segundos en completar la vuelta de

un circuito tipo Endurance.

La diferencia entre el yaw rate idóneo que demanda el piloto y el real se observa en

el Gráfico 4. Por sí solo, el coche es capaz de alcanzar los valores ideales en todo el circuito

excepto en unos pocos tramos, donde las curvas amarilla y azul no son coincidentes.

Gráfico 4: Comparación del yaw rate objetivo y el real (sin TV)

El par en ambos motores es igual y de la siguiente forma:

Gráfico 5: Par en los motores del vehículo (sin TV)

Estas simulaciones están realizadas con un setup subvirador, para que si el Torque

Vectoring deja de actuar en una curva el comportamiento del vehículo pase a ser

subvirador. Si el coche tuviera un setup neutro, podría ocurrir que al dejar de actuar el TV

el piloto perdiese más fácilmente el control del coche, ya que el comportamiento podría

pasar de neutro a sobrevirador con relativa facilidad.

Para conseguir este setup sobrevirador se han aumentado los valores de rigidez de

la antiroll bar delantera y de los muelles delanteros, añadiendo un multiplicador a sus

valores naturales, accediendo desde “Parameters > Car > Suspensions”.

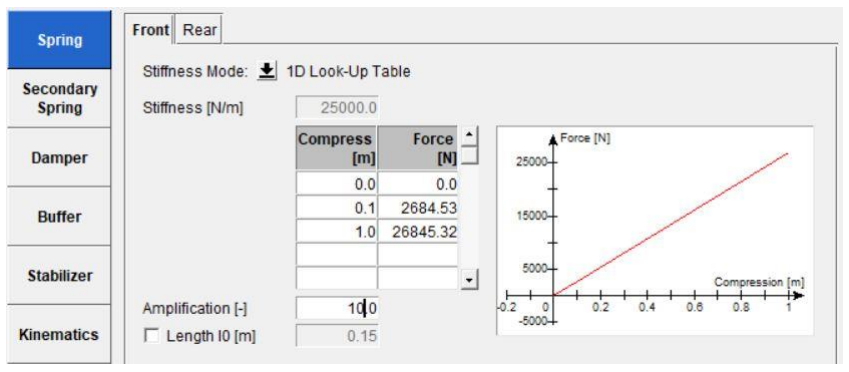
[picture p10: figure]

Figura 46: Parametrización de muelles de suspensión

Figura 47: Parametrización de ARBs

Los valores de los parámetros de control se han determinado por iteración,

observando los resultados obtenidos en diferentes simulaciones y eligiendo la combinación

que arroja mejores resultados.

Abreviatura | Parámetro | Valor
Kp | Ganacia proporcional | 1000
Ti | Tiempo integral | 0,1
Td | Tiempo derivativo | 0,4
Kp | Ganacia del anti-Windup | 2,5
Saturación | Saturación del anti-Windup | [1200; -1200] Nm
N | Ganancia del filtro | 0,5
Frec. corte | Frecuencia de corte del filtro | 15 rad/s

Tabla 2: Parámetros del controlador PID

El resultado obtenido ha sido el siguiente:

Figura 48: Simulación del TeR18 en Endurance (con TV)

El tiempo por vuelta ha bajado de 58,33 a 56,6 segundos, o lo que es lo mismo, se

ha reducido en 1,73 s el tiempo para una distancia recorrida de 775 m. Siendo la Endurance

una prueba de 22 km y suponiendo una ganancia constante e igual por vuelta, esto podría

significar una reducción del tiempo total de 49,11 segundos. Este resultado se acoge con

cierto escepticismo, ya que es muy complicado para un piloto de Formula Student mantener

unos tiempos por vuelta y una reducción del tiempo tan constantes como los supuestos

para realizar este último cálculo, por lo que la ganancia en pista será con casi total certeza

menor. Sin embargo, el resultado del cálculo invita al optimismo.

Usando la tabla de resultados de Formula Student Germany 2017 (incluida en el

anexo A3), donde el fstec17 concluyó la Endurance con un tiempo total de 1671,34

segundos, puede traducirse este resultado en puntos de competición. Teniendo en cuenta

la reducción de tiempo antes calculada, el resultado total habría sido de 1625,07 segundos,

lo cual hubiera aupado al equipo tres posiciones en la prueba y le habría dado alrededor

de 85 puntos.

La comprobación de que el controlador funciona se realiza mediante la gráfica de

yaw rate real frente a objetivo.

Gráfico 6: Comparación del yaw rate objetivo y el real (con TV)

En comparación con la gráfica anterior, el Yaw Rate medido coincide en casi todo

el gráfico con el valor del objetivo. Comprobando las señales de par en los motores, se

observa cómo se realiza la redistribución de par entre ambos.

Gráfico 7: Par en los motores del vehículo (con TV)

A continuación, se va a analizar por qué se produce la reducción de tiempo por

vuelta. Resulta evidente que si el coche recorre la misma distancia en menos tiempo es

porque va a mayor velocidad. Por tanto, una comparativa de velocidades en Matlab puede

arrojar luz sobre los puntos en los que el coche se beneficia en mayor y en menor medida

del torque vectoring implementado.

Gráfico 8: Comparación de velocidades con y sin TV

Como se puede observar, el coche recorre prácticamente todo el circuito a mayor

velocidad cuando el TV está activado que cuando está desactivado. Esto se debe a que la

mayor parte del circuito está formado por curvas, que es donde la lógica actúa y ayuda a

la conducción. De hecho, en las rectas (fácilmente reconocibles por ser los puntos donde

el coche acelera con más fuerza y alcanza mayor velocidad) el aumento de velocidad es

inexistente. Este efecto se observa claramente alrededor de los 150 y los 670 metros.

También es notorio que los mayores incrementos de velocidad se dan en torno a

los 200 y los 430 metros de recorrido. Estos tramos coinciden con curvas rápidas de radio

grande, y son aquellos en los que se aprecia una mayor corrección del yaw rate (Gráfico 4

y Gráfico 6). De aquí se puede concluir que la corrección del yaw rate a sus valores óptimos

tiene un impacto considerable en el desempeño del vehículo.

El aumento de la velocidad se produce gracias al incremento de la aceleración

lateral al tomar las curvas. Aunque la calidad del gráfico no es la mejor por las oscilaciones

de la señal, se puede apreciar la ganancia en aceleración lateral en la siguiente imagen.

Gráfico 9: Comparación de aceleración lateral con y sin TV

De nuevo, los dos puntos donde más aumenta la aceleración lateral son los mismos

tramos del circuito.

También es interesante observar las diferencias en la respuesta del piloto en

circuito. Con ellas se puede deducir el grado de confianza del piloto en el vehículo y su

facilidad de conducción: si acelera más o menos, si tiene que realizar giros más bruscos de volante, etc. Para ello se van a comparar la señal del pedal del acelerador y el volante

con y sin TV:

Gráfico 10: Comparación de % de acelerador pisado por el piloto con y sin TV

Gráfico 11: Comparación del ángulo de giro de volante con y sin TV

Los porcentajes de recorrido de acelerador pisado son muy parecidos, pero en las

dos curvas rápidas donde se observa la ganancia el aumento de % de acelerador es más

notorio. Esto puede ser porque el conductor no se asusta tan pronto con la reacción del

coche y se permite exigirle más, hasta que el vehículo empieza a mostrar comportamiento

inestable y el piloto afloja el acelerador.

Los giros de volante realizados por el piloto son ligeramente menos pronunciados

pero la diferencia no es muy destacable. Sí es reseñable que en los puntos destacados donde más actúa la lógica se dan pequeñas fluctuaciones en el giro del volante. Esto puede

ser debido a que, al ser la respuesta del coche poco natural o estar cerca de los límites de

controlabilidad del monoplaza, el piloto necesite realizar pequeñas correcciones. Sin

embargo, no son lo suficientemente grandes como para suponer un problema.

6.5.2 Análisis de Skidpad

Para analizar el desempeño del coche en la prueba de Skidpad se han utilizado las

mismas variables. Los valores de los parámetros del programa han sido los mismos que

para el circuito de Autocross y Endurance. Esto es debido a la intención de obtener una

lógica que sirva para todas estas pruebas, sin necesidad de realizar cambios en el

diagrama de bloques.

Hay que aclarar que los resultados obtenidos en las simulaciones de Skidpad tienen

una limitación importante: debido a la imposibilidad de definir dos vueltas a cada uno de

los círculos que componen el circuito, el coche sólo realiza el recorrido en forma de 8,

dando una vuelta en cada sentido.

Los resultados obtenidos sin torque vectoring han sido los siguientes:

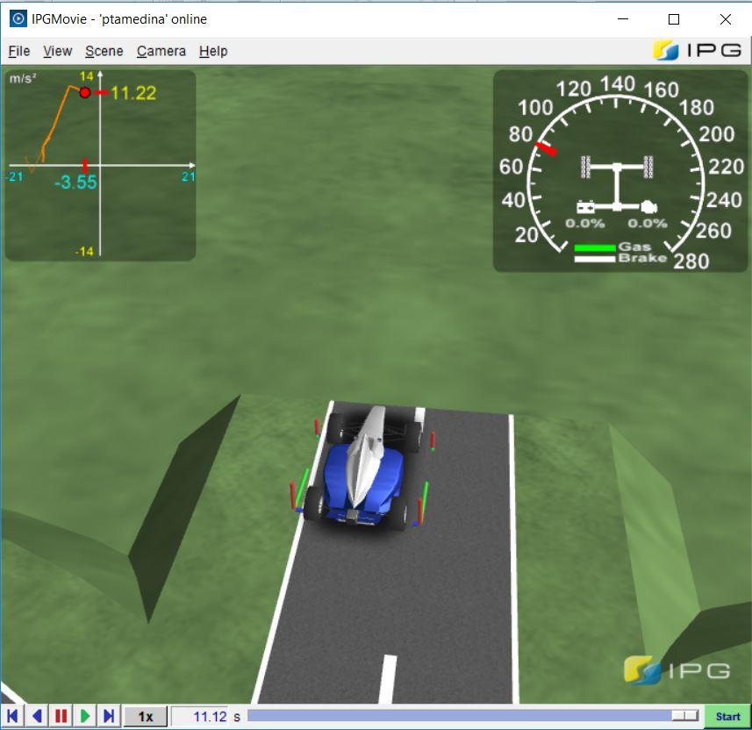
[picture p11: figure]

Figura 49: Simulación del TeR18 en Skidpad (sin TV)

Gráfico 12: Comparación del yaw rate objetivo y el real en Skidpad (sin TV)

Gráfico 13: Par en los motores del vehículo en Skidpad (sin TV)

Como se puede ver, el Yaw Rate real es superior al objetivo. Esto significa que el

coche sobrevira durante el Skidpad, pero en las simulaciones se aprecia que este efecto

no es suficiente como para que el piloto pierda el control del vehículo. Midiendo los tiempos

de la simulación manualmente, se obtienen los siguientes tiempos:

- Vuelta a izquierdas: 4,24 s
- Vuelta a derechas: 4,41 s
- Mejor tiempo: 4,24 s

Con el torque vectoring activo, los resultados han sido los siguientes:

Figura 50: Simulación del TeR18 en Skidpad (con TV)

Gráfico 14: Comparación del yaw rate objetivo y el real en Skidpad (con TV)

Gráfico 15: Par en los motores del vehículo en Skidpad (con TV)

En el Gráfico 14 se observa que en el Skidpad no se consigue controlar el yaw rate

de un modo tan fiable como en la Endurance. Sin embargo, se comprueba que funciona al

compararlo con el Gráfico 12, donde la diferencia entre yaw rate objetivo y real es mayor.

Los tiempos han sido:

- Vuelta a izquierdas: 4,11 s
- Vuelta a derechas: 4,20 s
- Mejor tiempo: 4,11 s

En esta prueba la mejora en tiempo es de 0,13 segundos. No obstante, los tiempos

obtenidos son mucho más rápidos que los obtenidos normalmente en las competiciones

de Formula Student. Al analizar la simulación, se encontró que el vehículo se salía de la

pista en determinados puntos del recorrido.

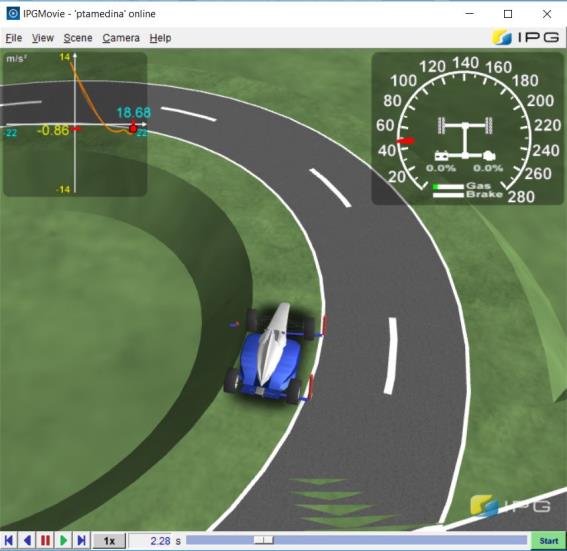
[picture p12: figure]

Figura 51: El coche fuera de pista durante la simulación.

Esta situación no debería darse ya que si el coche sale de la pista la simulación se

detiene y da error. Esto sólo sucede si la anchura de la pista se ajusta a la reglamentaria

del Skidpad. Con la anchura de pista por defecto, el coche no sale de los límites, aunque

los resultados en tiempos son similares.

Por estas razones, los resultados obtenidos en estas simulaciones no se tendrán

en cuenta y la ganancia en Skidpad se medirá en ensayos en pista una vez esté el

monoplaza terminado.

6.5.3 Test ISO 4138

Para analizar la respuesta del coche en función de la aceleración lateral a la que se

somete, se observa el giro de volante que el piloto ha tenido que realizar hasta que el

vehículo se vuelve inestable. Los resultados obtenidos han sido los siguientes:

Gráfico 16: Aceleración lateral frente a giro de volante en el test ISO 4138

Con el TV activado los resultados de la simulación son ilegibles en la zona inestable.

Sin embargo, pueden alcanzarse varias conclusiones de la observación de este gráfico.

Primeramente, la aceleración lateral máxima para la cual el comportamiento del

coche sigue siendo lineal es mayor. Sin torque vectoing activo, la aceleración lateral

comienza a ser no lineal alrededor de los 14 m/s²
, y cuando está activado la variación se

da alrededor de 16 m/s²
. Este cambio es muy positivo ya que proporciona al piloto la

capacidad de tomar curvas a mayor velocidad sin que el vehículo pierda estabilidad.

La segunda conclusión es que el gradiente de subviraje disminuye al activar el TV.

Esto se aprecia en la pendiente de la curva, que es menor, lo que posibilita conseguir una

aceleración lateral mayor para un mismo ángulo de giro de volante.

6.5.4 Elección de filtros y setup del coche

A la hora de programar, se ha tratado de elegir las características de cada bloque

y de colocarlos en el lugar idóneo para minimizar el valor del tiempo por vuelta.

Una de las necesidades primordiales de la lógica era que la señal que saliera a la

actuación tuviese el mínimo ruido posible. Para ello era necesario introducir filtros pasa-

baja en algún punto de la lógica, siendo dos las opciones más razonables: después de los

sensores o justo antes de enviar la señal de incremento de par a los motores. Colocar el

filtro al final aporta otra ventaja: al estar situado detrás del controlador en el diagrama,

puede eliminar las irregularidades surgidas en éste, mientras que los filtros tras los

sensores no serían capaces por estar situados en un punto anterior del diagrama.

Esta última ha sido la opción elegida tras analizar los tiempos por vuelta de ambas

alternativas y comprobar que con los filtros tras los sensores el coche era 1,3 segundos

más lento.

Figura 52: Simulación del TeR18 con filtros en los sensores

Gráfico 17: Comparación del yaw rate objetivo y el real con TV y filtros en los sensores

Se observa que con esta configuración la señal de yaw rate objetivo y la real tienen

un pequeño desfase. Esto puede deberse al retraso temporal que se introduce en la señal

de yaw rate de referencia al filtrar las variables necesarias para su cálculo.

Este retraso provoca que en el controlador la señal de yaw rate actual se compare

con la referencia calculada para un instante anterior, por lo cual la diferencia calculada no

es la adecuada y no se envía a los motores el par necesario para corregir adecuadamente

el yaw rate del vehículo.

Gráfico 18: Par en los motores del vehículo con TV y filtros en los sensores

Otro de los parámetros de los filtros que se ha modificado ha sido la frecuencia de

corte. Para realizar el Driver Adaption de Carmaker correctamente, es necesario que los

filtros tengan una frecuencia de 30 rad/s o mayor (aproximadamente 5 Hz), pero tras varias

pruebas se ha comprobado que el tiempo por vuelta es más bajo si se disminuye la

frecuencia de corte a 15 rad/s (aproximadamente 2,5 Hz) después de haber realizado la

adaptación. Este valor es el que se ha presentado en el apartado 6.5.1. Las imágenes

inferiores corresponden a las simulaciones llevadas a cabo con la frecuencia de corte de 5

Hz.

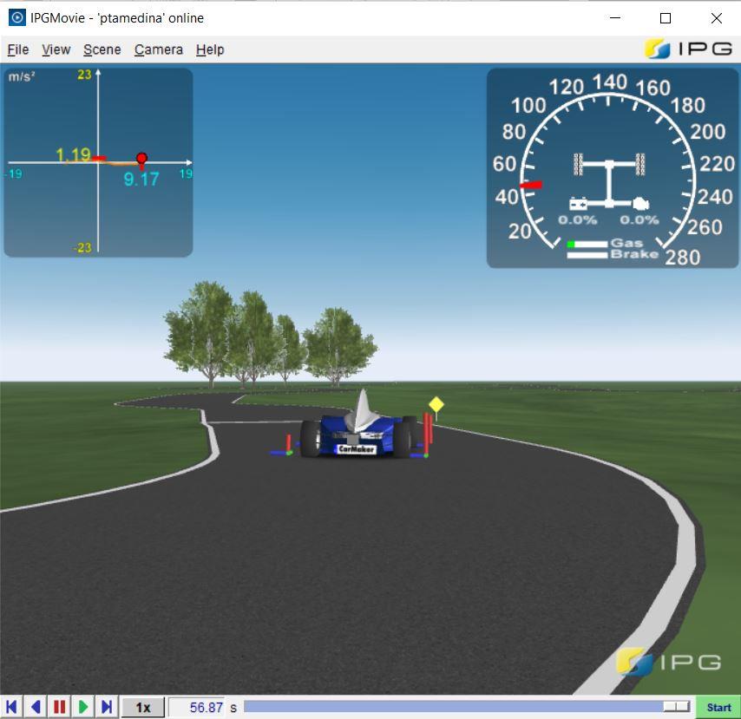
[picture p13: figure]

Figura 53: Simulación del TeR18 con frecuencia de filtrado 5 Hz

Gráfico 19: Par en los motores del vehículo con frecuencia de filtrado 5 Hz

El par entregado por los motores sufre oscilaciones indeseadas de hasta 40 Nm, lo

cual no ocurría con un filtro de 2,5 Hz. Por tanto, se elige filtrar la señal con una frecuencia

de corte de 2,5 Hz.

Por último, se ha comprobado el comportamiento del coche con un setup neutro

para compararlo con el setup subvirador antes simulado. Los resultados han sido los

siguientes con el TV desactivado:

Figura 54: Simulación del TeR18 con setup neutro (sin TV)

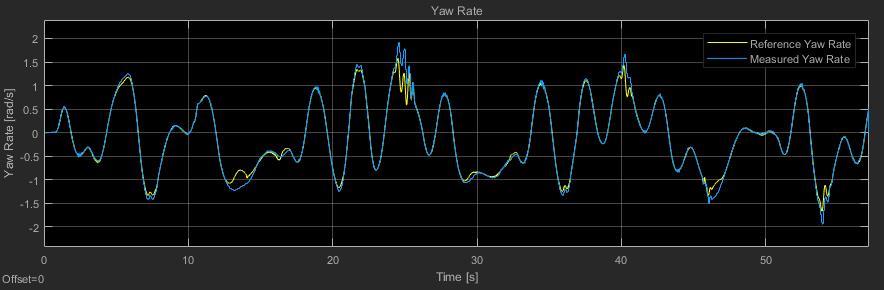
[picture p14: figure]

Gráfico 20: Comparación del yaw rate objetivo y el real con setup neutro (sin TV)

Y con TV activo:

Figura 55: Simulación del TeR18 con setup neutro (con TV)

Gráfico 21: Comparación del yaw rate ideal y objetivo con setup neutro (con TV)

Gráfico 22: Par en los motores del vehículo con setup neutro

La acción del control es menos evidente que para el caso del setup subvirador, e

incluso en algunos puntos el valor real se aleja más de la referencia cuando el torque

vectoring está activado. La disminución obtenida en el tiempo por vuelta es menor en este

caso: tan sólo 0,4 segundos.

## 7 VÍAS DE DESARROLLO

El presente Proyecto deja abiertas varias vías de desarrollo en el campo de la

modelización y el control orientados a la dinámica vehicular. Las principales son las

siguientes:

- Desarrollo de un traction control para implementación en el monoplaza de

Formula Student de Tecnun eRacing.

- Desarrollo de diferentes lógicas de control/tipos de controladores para

torque vectoring y traction control.

- Desarrollo de una lógica de control para vehículos 4WD y/o con

regeneración de energía.

- Desarrollo de un algoritmo de control adaptativo, en el que las ganancias del

PID se calculen en función de la situación de conducción.

- | Modelado | de | diferentes | tipos | de | diferencial | (abierto, | soldado,

autoblocante…).

- Modelado completo de un neumático en Matlab/Simulink.

El desarrollo de cualquiera de estas líneas de trabajo supondría un complemento

de gran interés al algoritmo presentado en este proyecto.

## 8 RESULTADO DEL PROYECTO

Este proyecto ha servido para profundizar en conocimientos tanto de dinámica

vehicular como de sistemas de control y de programación en bloques

El resultado del proyecto es una lógica de torque vectoring programada en Simulink

lista para ser instalada en el monoplaza de Tecnun eRacing. Con ella se espera lograr una

disminución en los tiempos en los que se llevan a cabo las pruebas de las competiciones

de Formula Student, y con ello unas mejores puntuaciones en las mismas.

Aunque los resultados obtenidos no alcanzan los propuestos en los objetivos al

inicio del proyecto, en parte por lo ambicioso de los mismos, el haber desarrollado una

herramienta que promete mejorar el rendimiento del monoplaza y que abre el camino al

desarrollo de controles cada vez mejores es motivo de satisfacción para el autor.

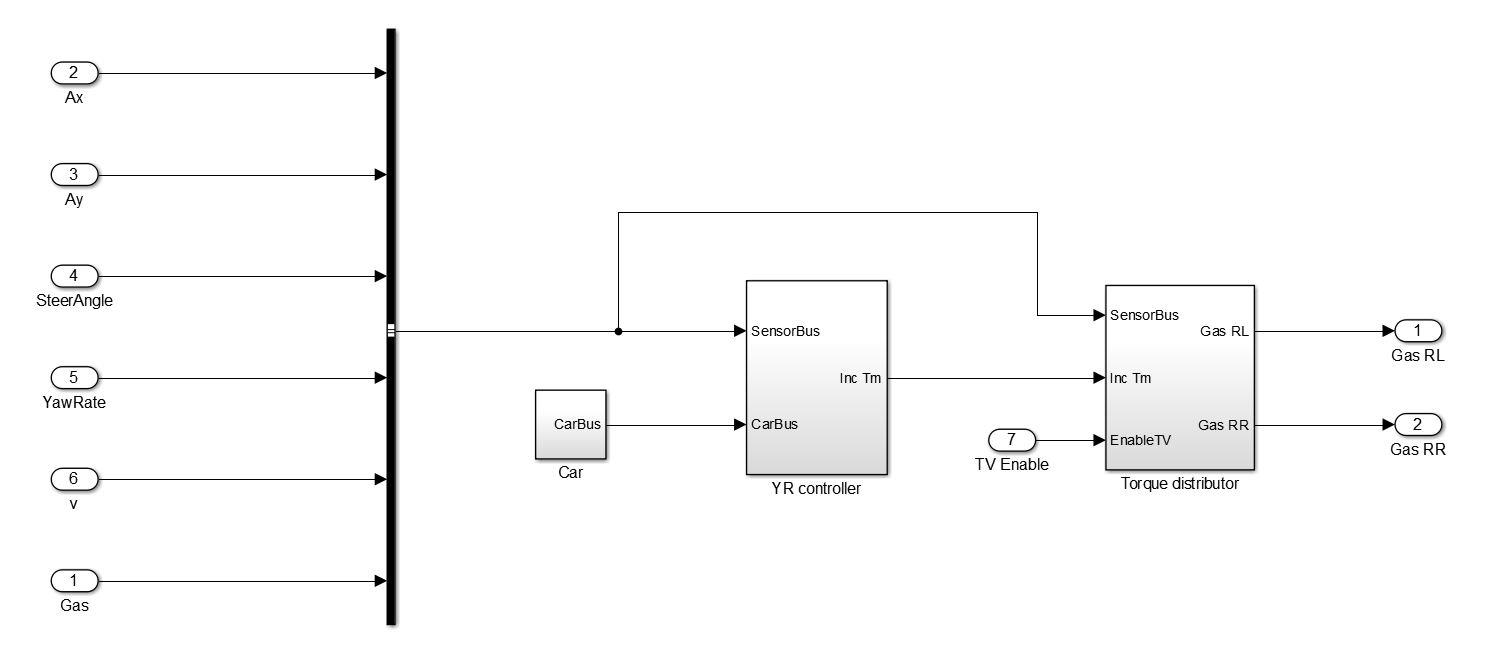
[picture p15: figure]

Figura 56: La lógica de TV que se implementará finalmente en el TeR18

A pesar de las numerosas simulaciones realizadas, será necesario validar el torque

vectoring en pista en una situación de conducción real. Al probar el coche con la lógica

implementada surgirán casi con total seguridad variaciones en los resultados derivadas de

factores que no se tienen en cuenta al simular.

Corregir estas desviaciones supondrá un reto adicional para poder presentar el

TeR18 en las mejores condiciones para competir.

## 9 PRESUPUESTO

En este apartado se desglosan los costes del Proyecto.

### 9.1 Presupuesto de inmovilizado

Cantidad | Referencia | Descripción

Precio (€)

| | | Unitario | Total

Total
inmovilizado | | | | 0

Tabla 3: Presupuesto de inmovilizado

### 9.2 Presupuesto de material fungible

Cantidad | Referencia | Descripción

Precio (€)

| | | Unitario | Total
1 | Impresión | Proyecto | 70 | 70
Total fungibles | | | | 70

Tabla 4: Presupuesto de material fungible

### 9.3 Presupuesto de equipamiento

Equipamiento

Cuota
adquisición
(€)

Tiempo
amortización
(años)

Cuota
amortización
mensual (€)

Tiempo
de uso
(mes)

Amortización
(€)
Ordenador | 500 | 4 | 10,42 | 6 | 62,5

Total
equipamiento | | | | | 62,5

Tabla 5: Presupuesto de equipamiento

### 9.4 Presupuesto de software

Software

Cuota
adquisición
(€)

Tiempo
amortización
(años)

Cuota
amortización
mensual (€)

Tiempo de
uso (mes)

Amortización
(€)
IPG Carmaker | 75000 | 4 | 1562,5 | 6 | 9375
Matlab | 5000 | 4 | 104,17 | 6 | 625,02
Windows 10 | 260 | 4 | 5,41 | 6 | 32,46
Total software | | | | | 10032,48

Tabla 6: Presupuesto de software

### 9.5 Presupuesto de mano de obra

Tarea | Duración
| (horas)

Precio (€)

| | Unitario | Total
Alumno | 300 | 3,12 | 936
Supervisor | 300 | 50 | 15000

Total mano
obra | | | 15936

Tabla 7: Presupuesto de mano de obra

### 9.6 Resumen del presupuesto

Se presenta a continuación el presupuesto global del proyecto, cuyo coste asciende

a 29259,08 €.

Partida

Importe (€)

| Parcial | Acumulado
Inmovilizado | 0 | 0
Fungibles | 70 | 70
Equipamiento | 62,5 | 132,5
Software | 10032,48 | 10164,98
Mano de obra | 15936 | 26100,98
Costes indirectos (10%) | | 2610
Total sin IVA | | 28710,98
Total con IVA | | 29259,08

Tabla 8: Resumen del presupuesto

## 10 REFERENCIAS

Gillespie, Thomas D. (1992) Fundamentals of Vehicle Dynamics. SAE Inc.

Milliken, William F. y Milliken, Douglas L. (1995) Race Car Vehicle Dynamics. SAE

International

Rubio Grijalva, Carlos (2017) Parametrization and Simulation of an Electric FSAE

Racecar

Aperribay Echave, Javier (2017) Desarrollo de Actualizaciones, Mejoras y

Acondicionamiento del Banco de Potencia de Motores de Combustión Interna

Ghosh, J., Tonoli, A. y Amati, N. (2015) A Torque Vectoring Strategy for Improving

the Performance of a Rear Wheel Drive Electric Vehicle

Ghosh, J., Tonoli, A. y Amati, N. (2017) Improvement of Lap-Time of a Rear Wheel

Drive Electric Racing Vehicle by a Novel Motor Torque Control Strategy

Hahn, C. (2017) Torque Vectoring – KIT Team Sharing Vehicle Control Success

Story | [online] | Matlab | and | Simulink | Racing | Lounge. | Available | from:

https://blogs.mathworks.com/racing-lounge/2017/11/22/torque-vectoring-ka-race-

ing/

Hahn, C., Muusers, D. and van Dijk, T. (2014) From Model to Racing in Five Minutes

[online] | Matlab | and | Simulink | Racing | Lounge. | Available | from:

https://es.mathworks.com/videos/matlab-and-simulink-racing-lounge-from-model-

to-racing-in-5-minutes-101289.html

Hahn, C., Maile, F. and Rudolf, V. (2014) Torque Vectoring – Controller Design,

Tuning and Testing [online] Matlab and Simulink Racing Lounge. Available from:

https://es.mathworks.com/videos/matlab-and-simulink-racing-lounge-torque-

vectoring-controller-design-tuning-and-testing-100567.html

## A ANEXOS

### A.1 Diagramas de bloques TV

Figura 57: Bloque E-Gas E-Motor correspondiente a la asignación de par motor de Carmaker for Simulink

Figura 58: Bloque de Torque Vectoring

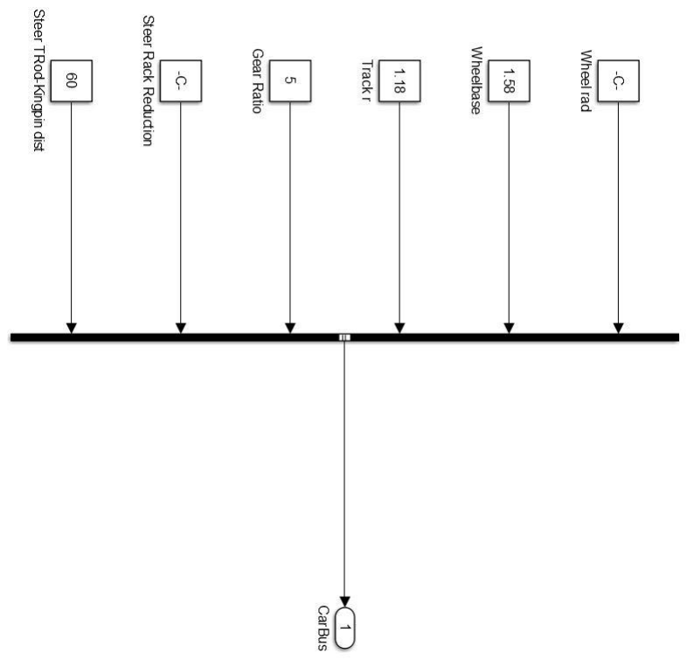
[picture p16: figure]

Figura 59: Bloque Car con parámetros del vehículo

Figura 60: Bloque YR controller

Figura 61: Bloque YR ref calculator

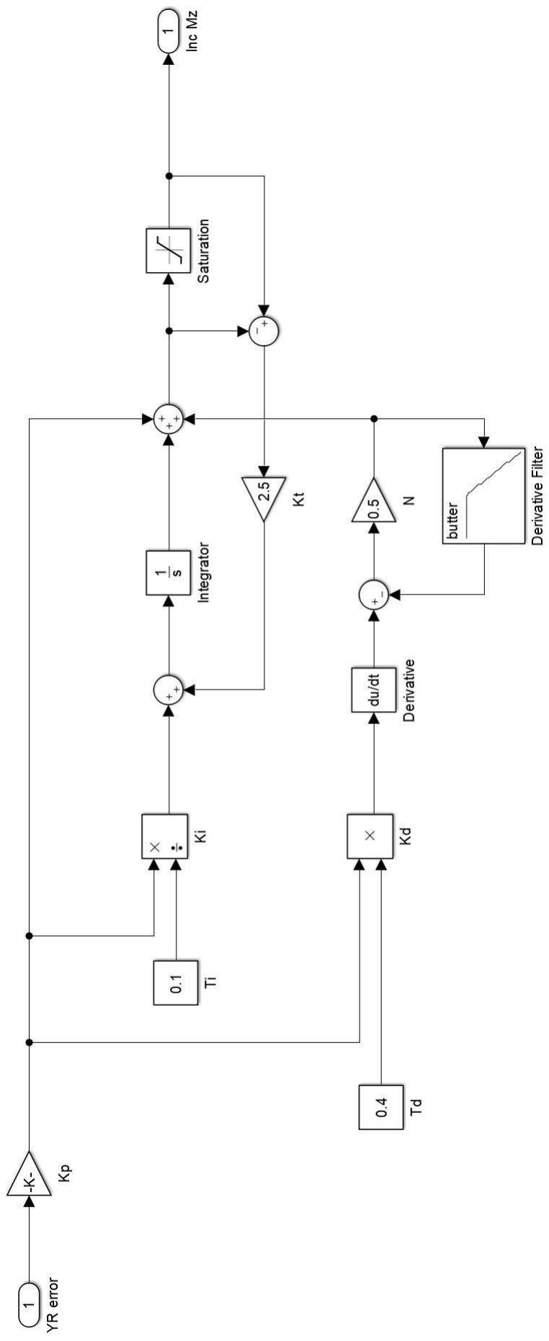
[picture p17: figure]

Figura 62: Bloque PID

Figura 63: Bloque Torque Distributor

### A.2 Diagramas de bloques de TC (descartados)

Figura 64: Algoritmo de control de ax

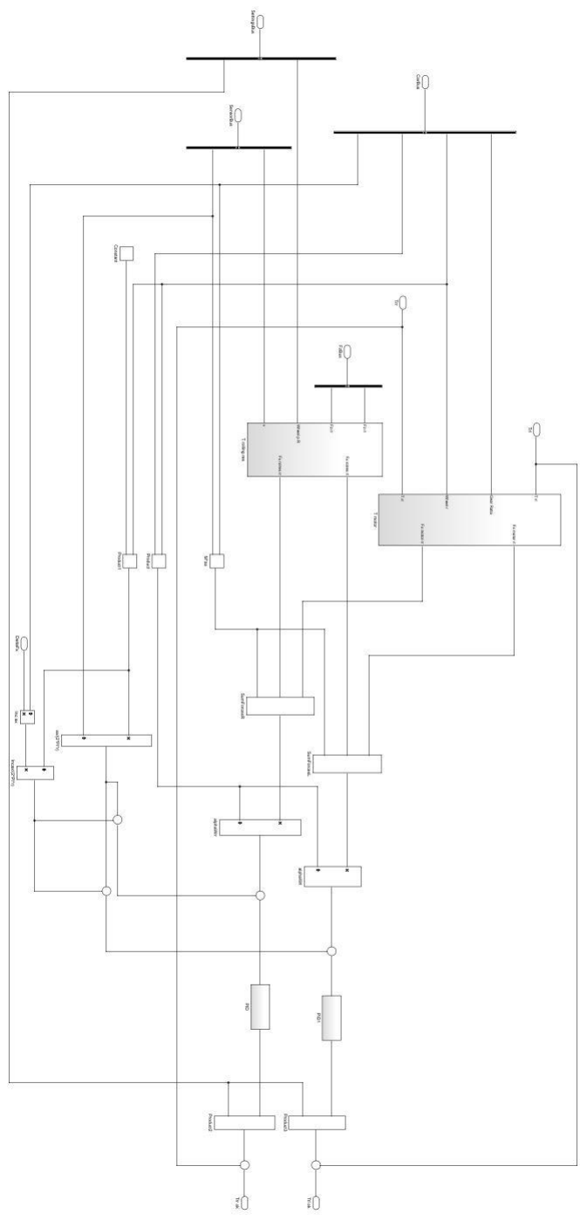
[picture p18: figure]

Figura 65: Bloque de Traction Control (ax)

Figura 66: Bloque Fx motor

Figura 67: Bloque Fx rolres

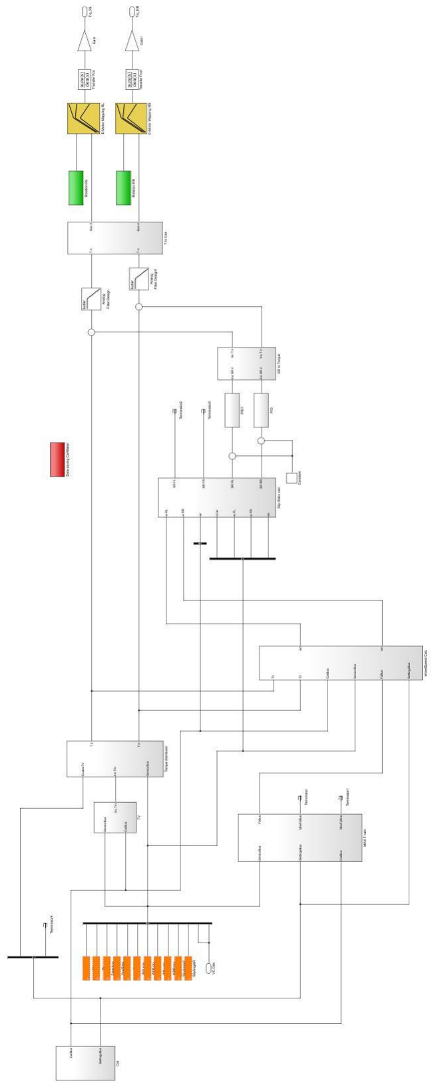
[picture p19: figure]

Figura 68: Algoritmo de control de slip ratio

Figura 69: Bloque MaxFx calc

Figura 70: Bloque Load transfer calc

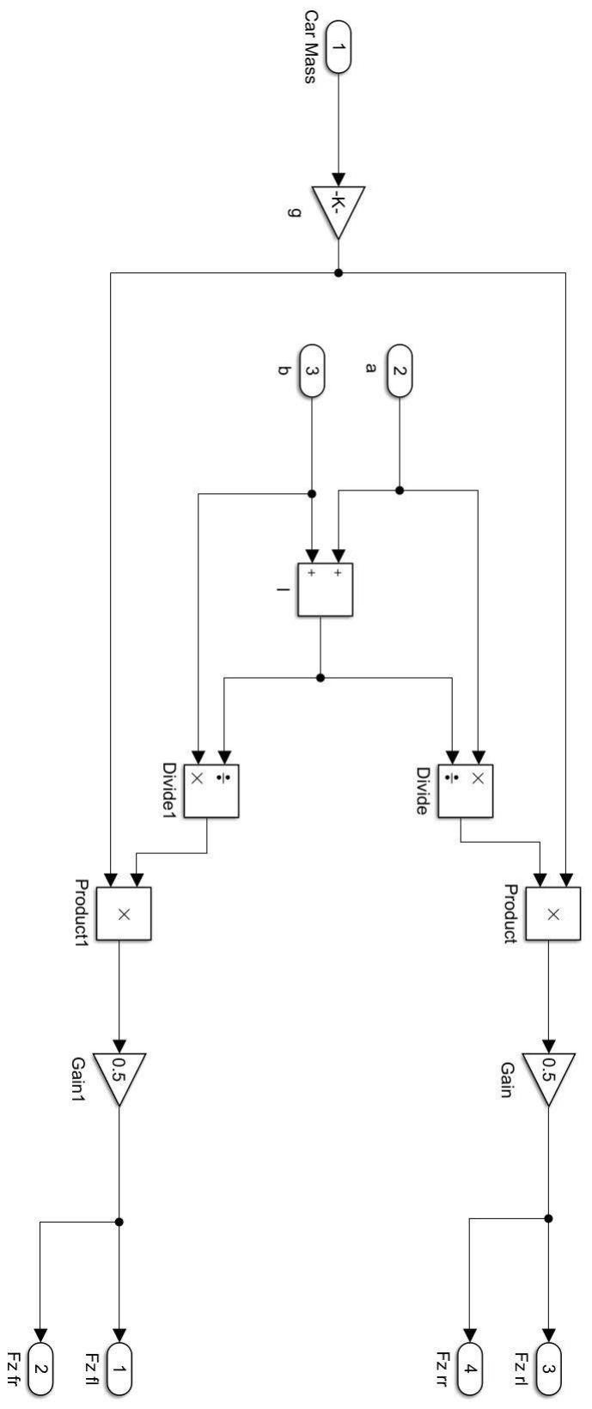
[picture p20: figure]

Figura 71: Bloque Static load calc

Figura 72: Bloque Long load transf

Figura 73: Bloque Lat load transf

Figura 74: Bloque Due to CG pos

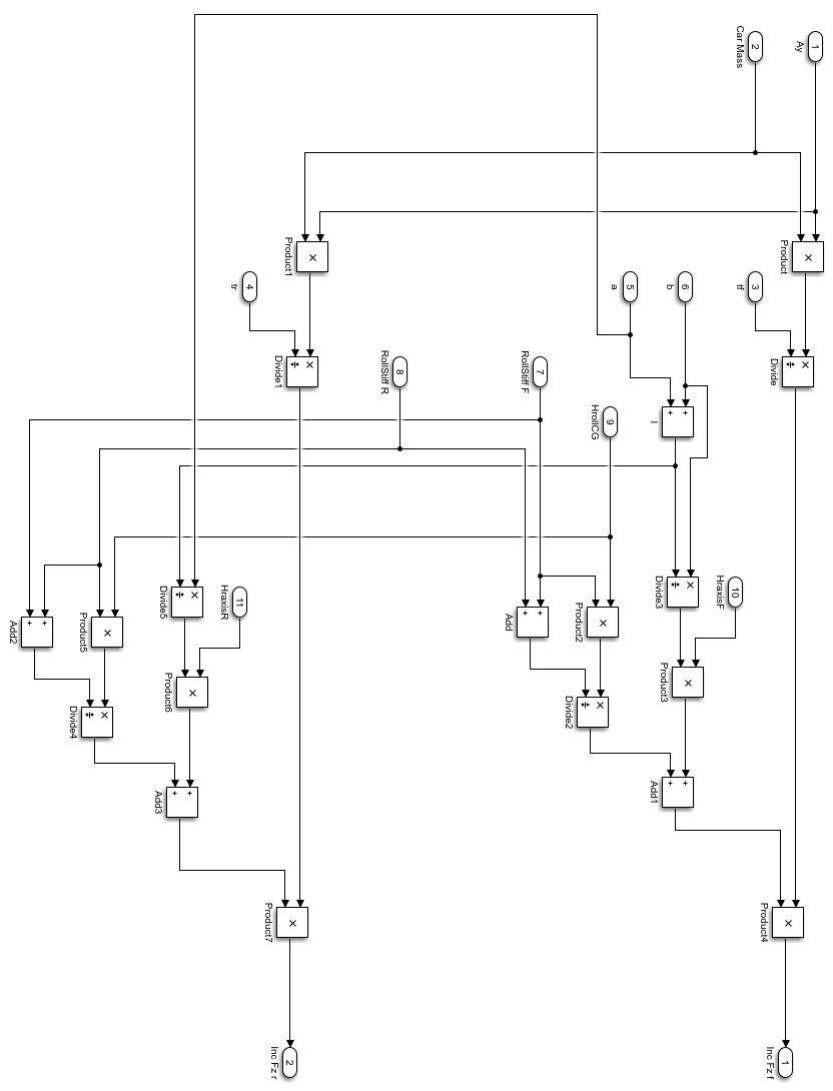
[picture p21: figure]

Figura 75: Bloque Due to roll

Figura 76: Bloque SR calc

Figura 77: Bloque Max F Tire

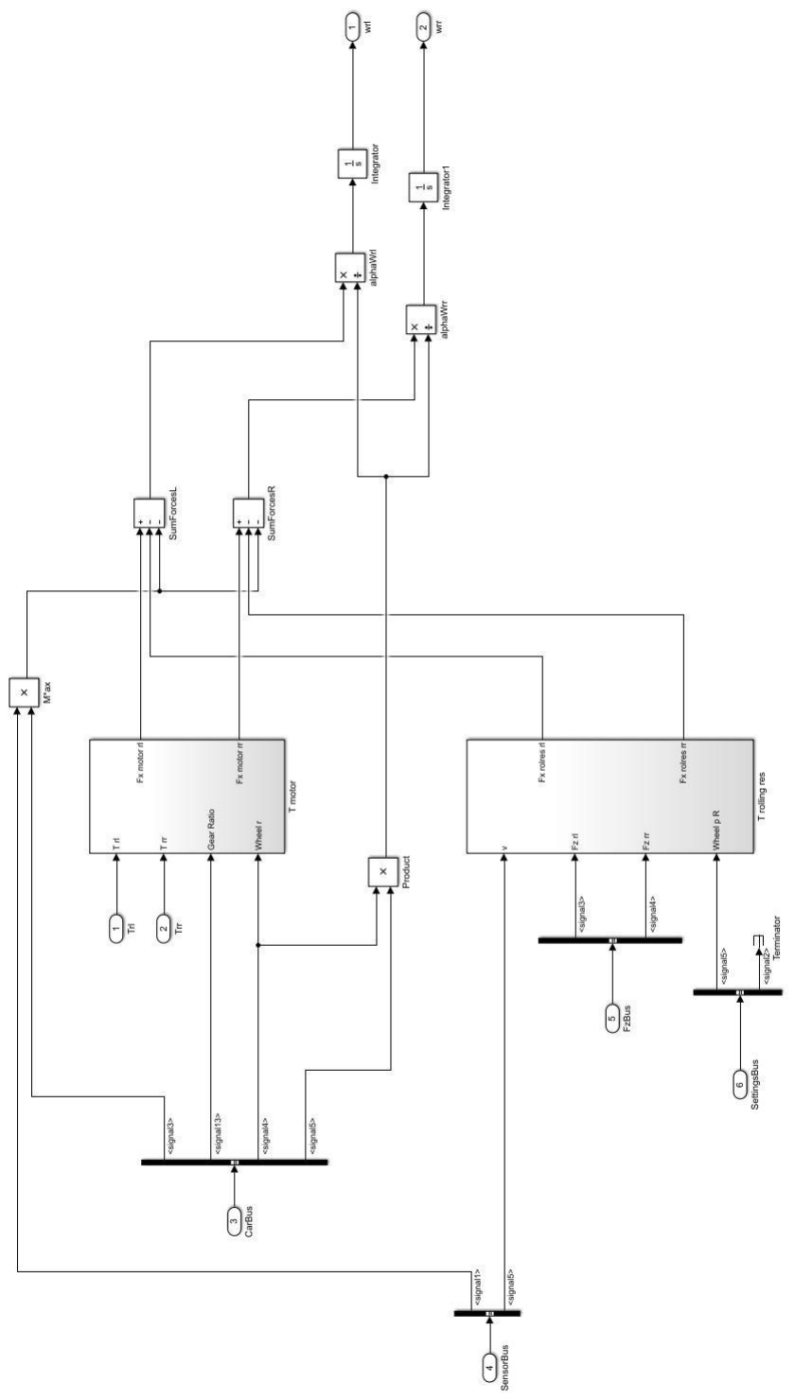
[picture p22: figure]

Figura 78: Bloque wheelSpeed Calc

Figura 79: Algoritmo de control de limitación de par motor

Figura 80: Bloque Limit Torque Calculation

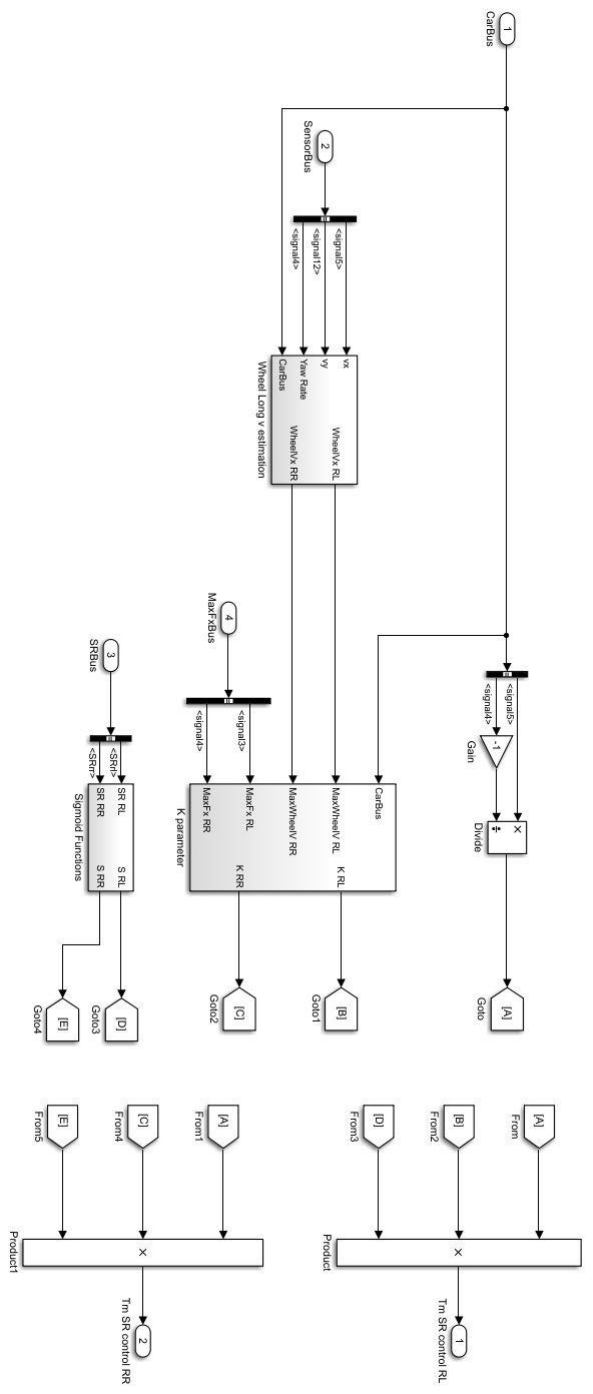
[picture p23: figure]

Figura 81: Bloque Slip Ratio Control

Figura 82: Bloque Wheel Long v estimation

Figura 83: Bloque K parameter

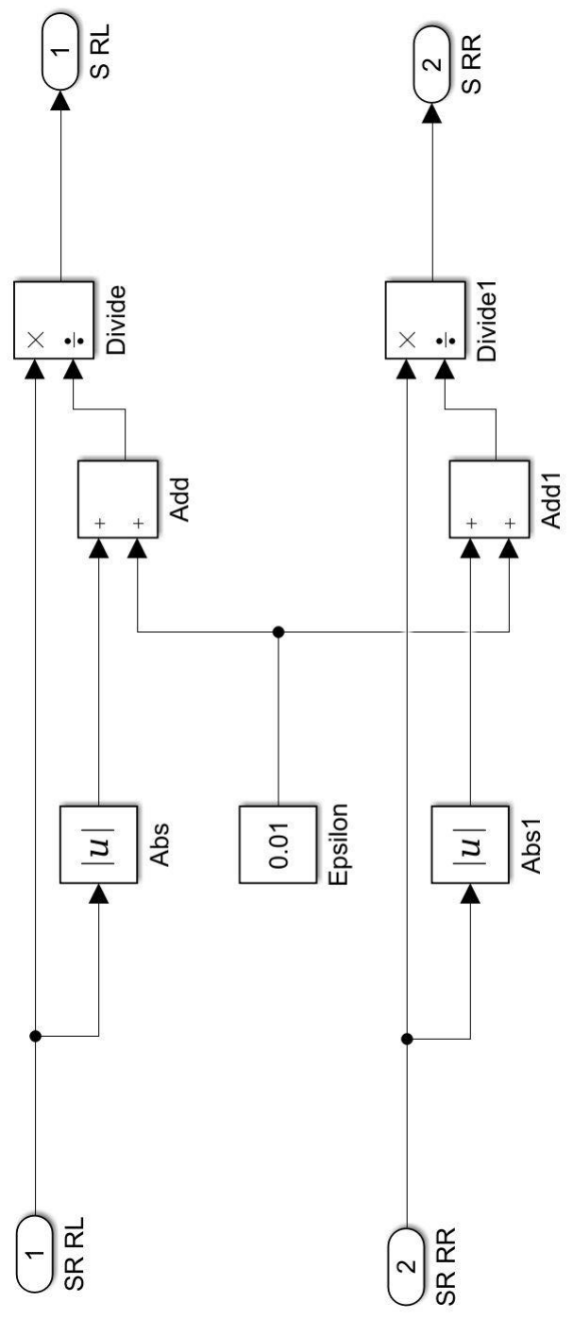
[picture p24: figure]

Figura 84: Bloque Sigmoid function

### A.3 Resultados de Endurance de FSG 2017

Figura 85: Resultados en la prueba de Endurance de FSG 2017

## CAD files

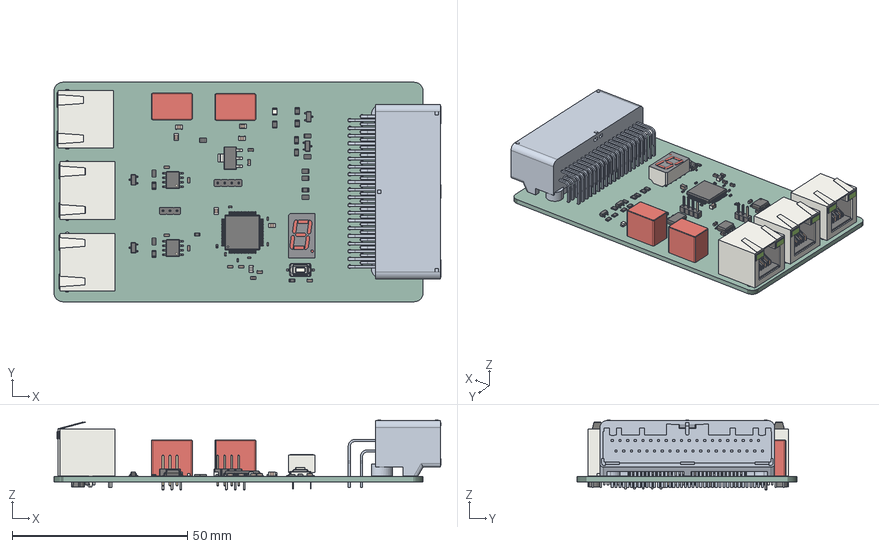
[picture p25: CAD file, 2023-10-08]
HARDWARE/TeR_ECU/TeR_ECU.step
110.5 x 62.7 x 19.9 mm
TeR_ECU PCB

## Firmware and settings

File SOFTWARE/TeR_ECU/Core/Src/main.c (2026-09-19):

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
/* Includes ------------------------------------------------------------------*/
#include "main.h"
#include "cmsis_os.h"
#include "adc.h"
#include "can.h"
#include "dma.h"
#include "i2c.h"
#include "iwdg.h"
#include "tim.h"
#include "usart.h"
#include "usb_device.h"
#include "gpio.h"

/* USER CODE BEGIN Includes */
#include "TeR_CAN.h"
#include "TeR_STATEMACHINE.h"
/* USER CODE END Includes */


void SystemClock_Config(void);
void MX_FREERTOS_Init(void);
static void MX_NVIC_Init(void);
/**
  * @brief  The application entry point.
  * @retval int
  */
int main(void)
{

  /* MCU Configuration--------------------------------------------------------*/

  /* Reset of all peripherals, Initializes the Flash interface and the Systick. */
  HAL_Init();

  /* Configure the system clock */
  SystemClock_Config();

  /* USER CODE BEGIN SysInit */
	/*Prevents  scs Timebase  from incrementing when hitting a braekpoint (No te da error despues de ver un breakpoint) */
	__HAL_DBGMCU_FREEZE_TIM5();
	__HAL_DBGMCU_FREEZE_IWDG();

  /* USER CODE END SysInit */

  /* Initialize all configured peripherals */
  MX_GPIO_Init();
  MX_DMA_Init();
  MX_CAN1_Init();
  MX_CAN2_Init();
  MX_TIM5_Init();
  MX_TIM13_Init();
  MX_IWDG_Init();
  MX_ADC1_Init();
  MX_I2C1_Init();
  MX_TIM3_Init();
  MX_USART1_UART_Init();
  MX_I2C2_Init();

  /* Initialize interrupts */
  MX_NVIC_Init();
  /* USER CODE BEGIN 2 */
	MX_USB_DEVICE_Init();

	initSCS(&htim5); //Arranca las systemCritical signals
	initCAN(&hcan2, &hcan1); //Arranca los can de inverters y main
  /* USER CODE END 2 */

  /* Init scheduler */
  osKernelInitialize();  /* Call init function for freertos objects (in cmsis_os2.c) */
  MX_FREERTOS_Init();

  /* Start scheduler */
  osKernelStart();

  /* We should never get here as control is now taken by the scheduler */

  /* Infinite loop */
  /* USER CODE BEGIN WHILE */
	while (1) {

    /* USER CODE END WHILE */

    /* USER CODE BEGIN 3 */
	}
  /* USER CODE END 3 */
}

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
/* USER CODE BEGIN 4 */
int _write(int file, char *ptr, int len) {
	//CDC_Transmit_FS((uint8_t*) ptr, len);  // Send data via USB CDC
	return len;
}
/* USER CODE END 4 */

/**
  * @brief  Period elapsed callback in non blocking mode
  * @note   This function is called  when TIM1 interrupt took place, inside
  * HAL_TIM_IRQHandler(). It makes a direct call to HAL_IncTick() to increment
  * a global variable "uwTick" used as application time base.
  * @param  htim : TIM handle
  * @retval None
  */
void HAL_TIM_PeriodElapsedCallback(TIM_HandleTypeDef *htim)
{
  if (htim->Instance == TIM1)
  {
    HAL_IncTick();
  }
}

/**
  * @brief  This function is executed in case of error occurrence.
  * @retval None
  */
void Error_Handler(void)
{
  /* USER CODE BEGIN Error_Handler_Debug */
	/* User can add his own implementation to report the HAL error return state */
	__disable_irq();
	while (1) {
	}
  /* USER CODE END Error_Handler_Debug */
}
#ifdef USE_FULL_ASSERT
/**
  * @brief  Reports the name of the source file and the source line number
  *         where the assert_param error has occurred.
  * @param  file: pointer to the source file name
  * @param  line: assert_param error line source number
  * @retval None
  */
void assert_failed(uint8_t *file, uint32_t line)
{
  /* USER CODE BEGIN 6 */
  /* User can add his own implementation to report the file name and line number,
     ex: printf("Wrong parameters value: file %s on line %d\r\n", file, line) */
  /* USER CODE END 6 */
}
#endif /* USE_FULL_ASSERT */

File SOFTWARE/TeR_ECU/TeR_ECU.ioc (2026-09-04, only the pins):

Mcu.UserName=STM32F405VGTx
PA0-WKUP.GPIO_Label=AIN2
PA0-WKUP.Signal=ADCx_IN0
PA1.GPIO_Label=AIN3
PA1.Signal=ADCx_IN1
PA10.Signal=USART1_RX
PA11.Signal=USB_OTG_FS_DM
PA12.Signal=USB_OTG_FS_DP
PA13.Signal=SYS_JTMS-SWDIO
PA14.Signal=SYS_JTCK-SWCLK
PA2.GPIO_Label=AIN0
PA2.Signal=ADCx_IN2
PA3.GPIO_Label=AIN1
PA3.Signal=ADCx_IN3
PA9.Signal=USART1_TX
PB0.GPIO_Label=SYS_LED
PB0.Signal=GPIO_Output
PB1.GPIO_Label=ERR_LED
PB1.Signal=GPIO_Analog
PB10.Signal=I2C2_SCL
PB11.Signal=I2C2_SDA
PB12.Signal=CAN2_RX
PB13.Signal=CAN2_TX
PB2.GPIO_Label=IMU_LED
PB2.Signal=GPIO_Output
PB6.Signal=I2C1_SCL
PB7.Signal=I2C1_SDA
PB9.GPIO_Label=SC_EN
PB9.Signal=GPIO_Output
PC6.Signal=S_TIM3_CH1
PC7.Signal=S_TIM3_CH2
PC8.GPIO_Label=YELLOW
PC8.Signal=GPIO_Output
PC9.Signal=S_TIM3_CH4
PD0.Signal=CAN1_RX
PD1.Signal=CAN1_TX
PE0.GPIO_Label=DOUT3
PE0.Signal=GPIO_Output
PE1.GPIO_Label=DOUT2
PE1.Signal=GPIO_Output
PE2.GPIO_Label=DOUT1
PE2.Signal=GPIO_Output
PE3.GPIO_Label=DOUT0
PE3.Signal=GPIO_Output
PE4.GPIO_Label=DIN2
PE4.Signal=GPIO_Input
PE5.GPIO_Label=DIN1
PE5.Signal=GPIO_Input
PE6.GPIO_Label=DIN0
PE6.Signal=GPIO_Input
PE7.GPIO_Label=DIN3
PE7.Signal=GPIO_Input
PH0-OSC_IN.Signal=RCC_OSC_IN
PH1-OSC_OUT.Signal=RCC_OSC_OUT

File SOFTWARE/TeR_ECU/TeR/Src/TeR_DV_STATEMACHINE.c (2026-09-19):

/*
 * TeR_DV_STATEMACHINE.C
 *
 *  Created on: Jan 31, 2026
 *      Author: pieroebs
 *
 *      Lógica de todo lo relacionado con la obtención y configuración del AS
 *
 *      -> obtención de estado del AS
 *      -> controlar como se cambia de estado en el AS
 *      -> permite o no el uso de actuadores
 *      -> configuración del modo de conduccion del DV
 *      -> request de safety Line (SDC en fsg)
 *
 *
 *
 *
 */
#include "TeR_DV_STATEMACHINE.h"
#include "math.h"
#define MAX_STEER_LEFT_ANGLE 95.0
#define MAX_STEER_RIGHT_ANGLE -95.0
#define DEG2RAD (180.0/PI)
#define ACTUATOR2STEER (3.5)
void set_assi_yellow(uint8_t set);
void set_assi_blue(uint8_t set);
void toggle_assi_yellow();
void toggle_assi_blue();

void permatask();
void dv_stateLoop();
void set_steer_angle(float angle);
void unsafe_set_steer_angle(float angle);
void as_act_statemachine();
dv_act_state_t get_as_act_state();
extern osTimerId_t as_allowed_timerHandle;
extern osTimerId_t as_emergency_beep_timerHandle;
const static uint32_t task_period = 5;
persist_t ready_time; // persistencia que cuenta el tiempo que estamos en AS_READY
persist_t res_k2; // persistencia que cuenta el tiempo que "res k2" ha estado en 1
persist_t ext_ts; // persistencia que cuenta el tiempo que "boton ts dv" ha sido presionado
uint32_t emergency_beep_count; // contador de beeps de emergencia
dv_act_state_t dv_act_state = AS_ACT_OFF; // tengo que crear la señal de can luego lo hago todo

/*
 * This function delays the request for AS_DRIVING
 * Use: To delay any requests from the driverless computer for a period of time after entering AS_DRIVING (required by the rules)
 * Important, DO NOT block (osDelay for example) in any timer callback, read the manual
 *
 */
void as_allowed_timer_callback(void *argument) {
	if (TeR.dv_system_status.as_status == AS_DRIVING) { // imaginate el caso en el que entras en driving, se lanza el timer, y antes de 3 segundos hay fallo, esto previene jittering (5ms coche en driving y luego cae)
		TeR.status.as_allowed = 1;
		TeR.dv_system_status.steering_state =
		TER_DV_SYSTEM_STATUS_STEERING_STATE_AVAILABLE_CHOICE;
	}
}

/*
 * This timer executes the beep the buzzer at a frequency that i forgot for around 8-10 seconds
 * The timer gets called every 200ms, when an internal count value is reached, the timer gets deactivated
 *
 *
 */
void as_emergency_beep_timer_callback(void *argument) {
	if (TeR.dv_system_status.as_status == AS_EMERGENCY) {
		HAL_GPIO_TogglePin(DOUT1_GPIO_Port, DOUT1_Pin);
		emergency_beep_count++;
		if (emergency_beep_count >= 40) {
			emergency_beep_count = 0;
			HAL_GPIO_WritePin(DOUT1_GPIO_Port, DOUT1_Pin, GPIO_PIN_RESET); // asegurar que la hemos apagado
			osTimerStop(as_emergency_beep_timerHandle);
		}
	}
	else{
		HAL_GPIO_WritePin(DOUT1_GPIO_Port, DOUT1_Pin, GPIO_PIN_RESET);
	}
}

//K2 o K3 se pueden usar como go signal (fsg 2026)
/*
 * This function gets the state of the DV statemachine, it follows the rule T 14.8
 * fully combinational, as expected by FSG
 * It has to be this way, as we have to implement as the rule says, please check the rules
 *
 * (puede que la haya liado en alguna condicion luego reviso) todo
 *
 */
dv_state_t get_dv_state() { // fsg 2026 T 14.8
	dv_state_t dv_state = AS_OFF;
	if ((TeR.asb_status.asb_ebs_state
			== TER_ASB_STATUS_ASB_EBS_STATE_ACTIVATED_CHOICE)
			|| (TeR.asb_status.asb_redundancy_state
					== TER_ASB_STATUS_ASB_REDUNDANCY_STATE_ACTIVATED_CHOICE)) {
		if ((TeR.dv_info.mission_status
				== TER_DV_INFO_MISSION_STATUS_FINISHED_CHOICE)
				&& (TeR.wheelInfo.speed <= 5)) { // supongo que quieren que este en emergency mientras se esta moviendo? ni idea? y si luego llegas a 0 entiendo que no deberia de latchearse? poco sentido la verdad, solo se guarda si el boton del res esta presionado
			if (!TeR.res_pdo_tx.e_stop_1 || !TeR.res_pdo_tx.e_stop_2) { // sl open at res ? (res abierto vamos)
				dv_state = AS_EMERGENCY;
			} else { // sl not open at RES
				dv_state = AS_FINISHED;
			}
		} else {
			dv_state = AS_EMERGENCY;
		}
	} else if ((TeR.dv_system_status.ami_state != 0) // si no es manual
	&& (TeR.status.asms)
			&& (TeR.asb_status.asb_ebs_state
					== TER_ASB_STATUS_ASB_EBS_STATE_INITIAL_CHECK_PASSED_CHOICE)
			&& (TeR.asb_status.asb_redundancy_state
					== TER_ASB_STATUS_ASB_REDUNDANCY_STATE_INITIAL_CHECK_PASSED_CHOICE)
			&& (TeR.status.state >= PRECHARGED)) { // >= precharged ya que a partir de este estado el TS está activo, que es lo que requiere la norma
		if (TeR.status.r2_d == 1) {
			dv_state = AS_DRIVING;
		} else if ((ter_bpps_bpps_decode(TeR.bpps.bpps) >= TeR.config.r2_d_brake)) {
			dv_state = AS_READY;
		}
	} else {
		dv_state = AS_OFF;
	}
	return dv_state;
}

/*
 *
 * Thread that controls the execution of the main DV statemachine
 *
 *
 * */

void dvStateMachine(void *argument) {
	uint32_t currentTick = osKernelGetTickCount();
	for (;;) {

		currentTick += task_period;
		osDelayUntil(currentTick);
		dv_stateLoop();
	}
}
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

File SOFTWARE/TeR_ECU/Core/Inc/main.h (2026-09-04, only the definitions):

#define DOUT1_Pin GPIO_PIN_2
#define DOUT1_GPIO_Port GPIOE
#define DOUT0_Pin GPIO_PIN_3
#define DOUT0_GPIO_Port GPIOE
#define DIN2_Pin GPIO_PIN_4
#define DIN2_GPIO_Port GPIOE
#define DIN1_Pin GPIO_PIN_5
#define DIN1_GPIO_Port GPIOE
#define DIN0_Pin GPIO_PIN_6
#define DIN0_GPIO_Port GPIOE
#define AIN2_Pin GPIO_PIN_0
#define AIN2_GPIO_Port GPIOA
#define AIN3_Pin GPIO_PIN_1
#define AIN3_GPIO_Port GPIOA
#define AIN0_Pin GPIO_PIN_2
#define AIN0_GPIO_Port GPIOA
#define AIN1_Pin GPIO_PIN_3
#define AIN1_GPIO_Port GPIOA
#define SYS_LED_Pin GPIO_PIN_0
#define SYS_LED_GPIO_Port GPIOB
#define ERR_LED_Pin GPIO_PIN_1
#define ERR_LED_GPIO_Port GPIOB
#define IMU_LED_Pin GPIO_PIN_2
#define IMU_LED_GPIO_Port GPIOB
#define DIN3_Pin GPIO_PIN_7
#define DIN3_GPIO_Port GPIOE
#define YELLOW_Pin GPIO_PIN_8
#define YELLOW_GPIO_Port GPIOC
#define SC_EN_Pin GPIO_PIN_9
#define SC_EN_GPIO_Port GPIOB
#define DOUT3_Pin GPIO_PIN_0
#define DOUT3_GPIO_Port GPIOE
#define DOUT2_Pin GPIO_PIN_1
#define DOUT2_GPIO_Port GPIOE

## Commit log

2023-09-02 Esquematicos CAN y Micro
    [CAN1.kicad_sch, CAN2.kicad_sch, Micro.kicad_sch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]
2023-09-03 Esquematico Micro para revisar
    [Micro.kicad_sch]
2023-09-04 Menos el del conector grande, los demas esquematicos acabados
    [CAN.kicad_sch, Deteccion_señales.kicad_sch, Functions.kicad_sch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]
2023-09-04 Falta conector tocho
    [CAN.kicad_sch, Micro.kicad_sch]
2023-09-05 Listo para empezar con layout
    [CAN.kicad_sch, Conector.kicad_sch, Deteccion_señales.kicad_sch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]
2023-09-05 Revisar y empezar Layout
    [CAN.kicad_sch, Conector.kicad_sch, Micro.kicad_sch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]
2023-09-10 añadido alimentacion datalogger
    [Conector.kicad_sch]
2023-09-10 Removed duplicate nested folder
    [CAN.kicad_sch, CAN1.kicad_sch, CAN2.kicad_sch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]
2023-09-12 Empezado el Layout
    [POWER.kicad_sch, TeR_ECU.kicad_pcb, UniPort.kicad_sch]
2023-09-13 Latout empezado
    [TeR_ECU.kicad_pcb]
2023-09-13 Contuinuando con Layout, micro hecha
    [Micro.kicad_sch, TeR_ECU.kicad_pcb]
2023-09-13 Seguir Layout, falta señales
    [TeR_ECU.kicad_pcb]
2023-09-14 Falta poco
    [Micro.kicad_sch, TeR_ECU.kicad_pcb]
2023-09-14 Falta Conector
    [Micro.kicad_sch, TeR_ECU.kicad_pcb]
2023-09-14 Falta pinear conector
    [Micro.kicad_sch, TeR_ECU.kicad_pcb, TeR_ECU.kicad_sch]
2023-09-14 Falata routear señales al conector
    [Conector.kicad_sch, TeR_ECU.kicad_pcb]
2023-09-14 Solo falta revisar
    [Conector.kicad_sch, Micro.kicad_sch, TeR_ECU.kicad_pcb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]
2023-09-15 Añadida resistencia luz de freno
    [Conector.kicad_sch, TeR_ECU.kicad_pcb]
2023-09-15 Rethought layout and footprints and fixed fuse normative problem
    [CAN.kicad_sch, Conector.kicad_sch, Deteccion_señales.kicad_sch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]
2023-09-16 Rethought layout and added pulldown to Horn mosfet
    [CAN1.kicad_sch, CAN2.kicad_sch, Functions.kicad_sch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]
2023-09-17 Layout V2, added 7-segment display, optimal placement of pins + rework of the boot headers(just one needed)
    [Conector.kicad_sch, Functions.kicad_sch, Micro.kicad_sch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]
2023-09-17 Added Board name/version and colaborators
    [TeR_ECU.kicad_pcb]
2023-09-18 Enlarged board to hold connector and added 3d files for cool render
    [TeR_ECU.kicad_pcb]
2023-09-18 Fixed Edge Cuts
    [TeR_ECU.kicad_pcb]
2023-09-18 finaly fixed borders
    [TeR_ECU.kicad_pcb]
2023-09-25 Rethought project using an STM32NucleoF7
    [Micro.kicad_sch, POWER.kicad_sch, RELAY.kicad_sch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]
2023-09-25 Replanteado layout con una F7
    [TeR_ECU.kicad_pcb]
2023-10-08 Cambiando micro
    [Micro.kicad_sch]
2023-10-08 Empezando Layout
    [Micro.kicad_sch, TeR_ECU.kicad_pcb]
2023-10-08 Layout acabado
    [Micro.kicad_sch, TeR_ECU.kicad_pcb, TeR_ECU.step]
2023-10-10 Acabado, falta 7-seg
    [TeR_ECU.kicad_pcb]
2023-10-13 Finished re layout and adaption between the two versions
    [Deteccion_señales.kicad_sch, Micro.kicad_sch, POWER.kicad_sch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]
2023-10-13 Generados archivos de produccion
    [TeR_ECU.kicad_pcb, bom.csv, designators.csv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]
2023-10-13 Cambiado valor fusible
    [POWER.kicad_sch, TeR_ECU.kicad_pcb, bom.csv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]
2023-10-14 Removed unnecesary via, DRC:Passes
    [Conector.kicad_sch, TeR_ECU.kicad_pcb, TeR_ECU.kicad_sch]
2023-10-23 Updated UNIPORT to fit the new 3 and 6 pin connected to PWR
    [TeR_ECU.kicad_pcb, UniPort.kicad_sch]
2023-11-09 Swapped Silkcreen of connectors, Inverters and main can Swapped
    [TeR_ECU.kicad_pcb]
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2024-01-02 Añadido y actualizado step
    [TeR_ECU.kicad_pcb]
2024-01-03 Cambio en el step para ayudar a mechanics
    [TeR_ECU.kicad_pcb]
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2024-01-09 Añadido delay para el horn. Hay que mirarlo porque no funciona bien.
2024-01-10 Solucionado el problema con el delay
    [main.c]
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2024-03-29 Refactored all TeR_CAN using STM32HAL callback functionality vastily simplifying code, added SCS handling and the Command-Response Subsystem
2024-03-30 Finished and tested, SCS, configured nvic to give priority to systick (HAL_Delay works now), started developing the torqueManager subsystem
2024-04-20 Loads of changes, filtro apañado para las lecturas buggy
    [TeR_CAN.c, TeR_ECU.ioc, TeR_SCS.c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]
2024-04-23 Microcontroller f405 sketch started
    [Micro.kicad_sch, POWER.kicad_sch, TeR_ECU.kicad_sch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]
2024-04-23 nrst doesnt need ressistance
    [microf405.kicad_sch]
2024-04-25 idea de esquema de safety y level shifter para señales de 24v
    [Conector.kicad_sch, TeR_ECU.kicad_sch, microf405.kicad_sch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]
2024-04-25 ic comments
    [Conector.kicad_sch, microf405.kicad_sch]
2024-04-29 sd añadida, uniport redundante eliminado
    [Conector.kicad_sch, SD.kicad_sch, TeR_ECU.kicad_sch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]
2024-06-15 usb-c, good debug conn, switch
    [CAN.kicad_sch, Conector.kicad_sch, Deteccion_señales.kicad_sch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]
2024-07-01 Quick fix, commit pls
    [TeR_STATEMACHINE.c]
2024-07-08 Quick typo
    [TeR_ECU.kicad_pcb]
2024-07-17 Kept improving schmatic for V2
    [CAN.kicad_sch, SD.kicad_sch, USB.kicad_sch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]
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2024-08-24 Quick changes
    [CAN.kicad_sch, Conector.kicad_sch, TeR_ECU.kicad_sch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]
2024-08-24 Advanced design and added IMU/GPS moduleç
    [CAN.kicad_sch, Conector.kicad_sch, Deteccion_señales.kicad_sch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]
2024-09-12 Advanced RF fronted BIAS-T for LNA antenna and digital input redesign
    [Deteccion_señales.kicad_sch, GPS.kicad_sch, INPUTS.kicad_sch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]
2024-10-17 Cool things
    [EEPROM.kicad_sch, IMU.kicad_sch, INPUTS.kicad_sch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]
2024-10-20 Quick changes, go to start layouting
    [CAN.kicad_sch, Conector.kicad_sch, EEPROM.kicad_sch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]
2024-10-20 Began layout
    [GPS.kicad_sch, IMU.kicad_sch, INPUTS.kicad_sch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]
2024-10-23 First layout prototype
    [CAN.kicad_sch, GPS.kicad_sch, INPUTS.kicad_sch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]
2024-11-03 Finished layout, RF design, and quick DRC check, Lookin gud
    [CAN.kicad_sch, Conector.kicad_sch, GPS.kicad_sch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]
2024-11-03 Improved Layout and hole placement
    [TeR_ECU.kicad_pcb]
2024-11-03 Corrected RF trace width inside pad
    [TeR_ECU.kicad_pcb]
2024-11-27 Added Diode to clamp usb pwr
    [RELAY.kicad_sch, TeR_ECU.kicad_pcb, TeR_ECU.kicad_sch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]
2024-11-27 Archivos de producción V2.0.0
    [TeR_ECU.kicad_pcb, TeR_ECU.kicad_sch]
2025-01-09 Prevent debugger from freezing IWDG
    [main.c]
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2025-02-11 broken commit working complementary filter for attitude and imu viewing script
    [TeR_ECU.ioc, TeR_INERTIAL.c, TeR_STATEMACHINE.c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]
2025-02-12 Improved code, removed unnecessary mutex, stateMachine refactor, broken commit
    [TeR_STATEMACHINE.c, TeR_STATEMACHINE.h]
2025-04-12 sitema de conffigs, toruqe vectoring tested, ya no crashea aparentemente
    [TeR_CAN.c, TeR_ECU.ioc, TeR_GPS.c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]
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2025-04-22 fixed funny i2c bug
    [TeR_ECU.ioc, TeR_INERTIAL.c, TeR_SERVOS.c]
2025-04-22 Added eeprom lib inc path and fixed 120R resistors in Hardware
    [CAN.kicad_sch, EEPROM.kicad_sch, GPS.kicad_sch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]
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2025-04-25 funny memory leak doble seta in torquevectoring, better handeling in deinit
    [TeR_CAN.c, TeR_COMMAND.c]
2025-04-25 VLA sizeof() does not return correct size, using precalculated length should fix
    [TeR_GPS.c]
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2025-07-10 softfault fix + cooling accu fans
    [TeR_GPS.c, TeR_STATEMACHINE.c]
2025-07-14 rework config system, eeprom read, eeprom clear and default function, servos operation
    [TeR_SERVOS.c, TeR_STATEMACHINE.c]
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2025-10-07 ecu CAN rework in progess
    [TeR_CAN.c, TeR_COMMAND.c, TeR_ECU.ioc]
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2026-01-30 [NOT WORKING] fixing stuff for DV
    [TeR_CAN.c, TeR_INERTIAL.c, TeR_STATEMACHINE.c]
2026-01-30 [NOT WORKING] metiendole al rework de esta baina para q se conduzca sola
    [TeR_CAN.c, TeR_STATEMACHINE.c]
2026-02-03 [NOT WORKING] fucking linker
    [TeR_CAN.c, TeR_COMMAND.c, TeR_DV_STATEMACHINE.c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]
2026-02-05 [NOT WORKING] avanzando con el dv
    [TeR_CAN.c, TeR_COMMAND.c, TeR_DV_STATEMACHINE.c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]
2026-02-06 [NOT WORKING] sdc relay is now a function of the state of multiple task
    [TeR_CAN.c, TeR_DV_STATEMACHINE.c, TeR_ECU.ioc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]
2026-02-07 [NOT WORKING] improving SL handling
    [TeR_COMMAND.c, TeR_DV_STATEMACHINE.c, TeR_SL.c]
2026-02-08 [NOT WORKING] updateing dv statemachine to something less schizo
    [TeR_CAN.c, TeR_COMMAND.c, TeR_DV_STATEMACHINE.c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]
2026-02-08 [NOT WORKING] rework in progress
    [TeR_COMMAND.c, TeR_DV_STATEMACHINE.c]
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2026-02-08 Revert "Switched to make"
    This reverts commit dcff453b13a250526cfad780517ccef26f82419c.
    [TeR_DV_STATEMACHINE.c, TeR_ECU.ioc, main.c]
2026-02-24 [Message scheduler + inverter bridge fixed]
    [TeR_CAN.c, TeR_STATEMACHINE.c]

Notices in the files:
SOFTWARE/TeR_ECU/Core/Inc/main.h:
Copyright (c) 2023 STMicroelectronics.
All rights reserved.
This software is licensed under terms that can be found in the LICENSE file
